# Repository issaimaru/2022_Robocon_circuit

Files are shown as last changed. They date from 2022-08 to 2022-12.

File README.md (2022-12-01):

# 2022_Robocon_circuit
**2022年ロボコンの回路**<br>
マスターブランチは保護されているので，各ブランチで必ずプルリクエストを送ってください．<br>

他にも[自作MD](https://github.com/Issaimaru/MoterDriver_v1)と[自作電源基板](https://github.com/Issaimaru/PowerSupply_v1)とか[モババ電源分岐させるやつ](https://github.com/Issaimaru/USB_JST-XH_CONVERTER)とかいろいろ使ったけど不具合多く見つかって成仏しそうになった<br>

回路図とピン配置をここに明記しておきます．<br>

- 上部機構
  - 回路図
    上部機構
    
    > **Warning**<br>
    > 回路図が一部変わっています．詳しくはIssaimaruまで...
  
  - ピン配置
  
    | ピン番号 | 機能 | 備考 |
    | :---: | :---: | :--: |
    | PB_8/D15 | I2C_SCL | MoterDriver-Controller v3との通信用(I2C)|
    | PB_9/D14 | I2C_SDA | 同様 |
    | PA_15 | UART_TX | 足回りのmbedとの通信用 |
    | PB_7 | UART_RX | 同様 |
    | PB_4/D5 | PWM1 | 上下機構のモータの制御用 |
    | PB_5/D4 | DIR1 | 同様 |
    | PB_10/D6 | PWM2 | 装填機構のモータの制御用 |
    | PB_3/D3 | DIR2 | 同様 |
    | PA_8/D7 | PWM3 | 射出機構のモータ制御用 |
    | PA_10/D2 | DIR3 | 同様 |
    | PA_1/A1 | LED1 | MDCとの通信確認用LED |
    | PA_4/A2 | LED2 | 足回りのmbedとの通信確認用LED |
    | PA_0/A0 | LED3 | 上下機構の速度確認用LED(PWMに対応) |
    | PB_0/A3 | LED4 | 上下機構の上昇確認用LED |
    | PC_1/A4 | LED5 | 上下機構の下降確認用LED |
    | PC_0/A6 | LED6 | 射出確認用LED |
    
- 足回り
  - 回路図
    足回り

    > **Warning**<br>
    > 回路図が一部変わっています．詳しくはIssaimaruまで...
    
  - ピン配置

    | ピン番号 | 機能 | 備考 |
    | :---: | :---: | :--: |
    | PB_8/D15 | I2C_SCL | MoterDriver-Controller v3との通信用(I2C)|
    | PB_9/D14 | I2C_SDA | 同様 |
    | PA_15 | TWE_TX | TWELITEとの通信用 |
    | PB_7 | TWE_RX | 同様 |
    | PA_12 | MCU_RX | 上部機構側mbedとの通信用 |
    | PA_11 | MCU_TX | 同様 |
    | PB_4/D5 | PWM1 | 三輪メカナムの正面側モータ制御用 |
    | PB_5/D4 | DIR1 | 同様 |
    | PB_10/D6 | PWM2 | 三輪メカナムの左側面側モータの制御用 |
    | PB_3/D3 | DIR2 | 同様 |
    | PA_8/D7 | PWM3 | 三輪メカナムの右側面側モータの制御用 |
    | PA_10/D2 | DIR3 | 同様 |
    | PA_0/A0 | LED1 | MDCとの通信確認用LED |
    | PA_1/A1 | LED2 | 上部機構側mbedとの通信確認用LED |
    | PA_4/A2 | LED3 | TWELITEとの通信確認用LED |
    
- 暴走対策機能付き非常停止スイッチ
  - 回路図
    暴走対策機能付き非常停止スイッチ

  - 接続方法<br>
    - INPUT1，INPUT2はPowerUnit BseriesのMILコネクタ部のうちのVCCとGNDに無理やりはんだ付けして配線を伸ばして2ピンのJST-XHで接続してください．
    - SW_INは非常停止スイッチと接続してください．
    - CTRLはPowerUnit BseriesのCTRLと接続してください．
    - SWITCHはPowerUnit BseriesのSWITCHと接続してください．
    
 - 上部機構用エンコーダー
  - 回路図
    上部機構用エンコーダー

  - ピン配置
    | ピン番号 | 機能 | 備考 |
    | :---: | :---: | :--: |
    | PB_7/D4 | I2C_SDA | メインマイコンとの通信用 |
    | PB_6/D5 | I2C_SCL | 同様 |
    | PF_0/D7 | ENC1_A | ロリコン1のA相 |
    | PF_1/D8 | ENC1_B | ロリコン1のB相 |
    | PA_8/D9 | ENC1_X | ロリコン1のX相 |
    | PA_11/D10 | ENC2_A | ロリコン2のA相 |
    | PB_5/D11 | ENC2_B | ロリコン2のB相 |
    | PB_4/D12 | ENC2_X | ロリコン2のX相 |
    | PB_1/D6 | PHOTO_OUT | フォトインタラプタの入力(HI->物体有/LOW->物体無) |
    | PA_6/A5 | RED | テープLEDの赤色点灯用ピン |
    | PA_4/A3 | GREEN | テープLEDの緑色点灯用ピン |
    | PA_3/A2 | BLUE | テープLEDの青色点灯用ピン |
    
  - 足回り用ロリコン
    - 回路図<br>
      足回り用ロリコン<br>

    - ピン配置<br>
      | ピン番号 | 機能 | 備考 |
      | :---: | :---: | :--: |
      | PB_7/D4 | I2C_SDA | メインマイコンとの通信用 |
      | PB_6/D5 | I2C_SCL | 同様 |
      | PA_12/D2 | ENC1_A | ロリコン1のA相 |
      | PB_0/D3 | ENC1_B | ロリコン1のB相 |
      | PF_0/D7 | ENC2_A | ロリコン2のA相 |
      | PB_1/D6 | ENC2_B | ロリコン2のB相 |
      | PF_1/D8 | ENC3_A | ロリコン3のA相 |
      | PA_8/D9 | ENC3_B | ロリコン3のB相 |
      | PB_5/D11 | ENC4_A | ロリコン4のA相 |
      | PA_11/D10 | ENC4_B | ロリコン4のB相 |
      
  - 国技館射出
    - 回路図<br>
      国技館射出<br>
      
    - ピン配置<br>
      | ピン番号 | 機能 | 備考 |
      | :---: | :---: | :--: |
      | PC_12 | UART1_TX | 足回りとの通信用 |
      | PD_2 | UART1_RX | 同様 |
      | 🌠PF_7 | UART2_TX | マトリクスLEDとの通信用 |
      | 🌠PF_6 | UART2_RX | 同様 |
      | 🌠PA_10 | PWM1 | モータ駆動用PWM出力ピン |
      | 🌠PB_3 | PWM2 | 同様 |
      | 🌠PB_5 | PWM3 | 同様 |
      | 🌠PB_4 | PWM4 | 同様 |
      | 🌠PA_3 | PWM5 | 同様 |
      | 🌠PA_2 | PWM6 | 同様 |
      | 🌠PC_7 | DIR1 | モータ回転方向信号出力ピン |
      | 🌠PA_9 | DIR2 | 同様 |
      | 🌠PA_8 | DIR3 | 同様 |
      | 🌠PB_10 | DIR4 | 同様 |
      | 🌠PA_7 | DIR5 | 同様 |
      | 🌠PB_6 | DIR6 | 同様 |
      | PD_5 | ENC1_B | ロリコン1のB相 |
      | PD_6 | ENC1_A | ロリコン1のA相 |
      | PD_7 | ENC2_B | ロリコン2のB相 |
      | PE_3 | ENC2_A | ロリコン2のA相 |
      | PF_1 | ENC3_B | ロリコン3のB相 |
      | PF_0 | ENC3_A | ロリコン3のA相 |
      | PD_1 | ENC4_B | ロリコン4のB相 |
      | PD_0 | ENC4_A | ロリコン4のA相 |
      | PG_0 | ENC5_B | ロリコン5のB相 |
      | PE_1 | ENC5_A | ロリコン5のA相 |
      | PG_9 | ENC6_B | ロリコン6のB相 |
      | PG_12 | ENC6_A | ロリコン6のA相 |
      | PD_14 | RED | テープLED 赤色 |
      | PD_15 | GREEN | テープLED 緑色 |
      | PE_9 | BLUE | テープLED 青色 |
      | PF_11 | LED1 | 確認用LED(任意) |
      | PE_0 | LED2 | 同様 |
      | PG_8 | LED3 | 同様 |
      | PG_5 | LED4 | 同様 |
      | PG_6 | LED5 | 同様 |

  - 国技館足回り
    - 回路図<br>
      国技館足回り<br>
      
    - ピン配置<br>
      | ピン番号 | 機能 | 備考 |
      | :---: | :---: | :--: |
      | PA_15 | UART1_TX | IM920sLとの通信用 |
      | PB_7 | UART1_RX | 同様 |
      | PA_11 | UART2_TX | 射出マイコンとの通信用 |
      | PA_12 | UART2_RX | 同様 |
      | D6/PB_10 | PWM1 | モータ駆動用PWM出力ピン |
      | D7/PA_8 | PWM2 | 同様 |
      | D8/PA_9 | PWM3 | 同様 |
      | D9/PC_7 | PWM4 | 同様 |
      | Pc_4 | DIR1 | モータ回転方向信号出力ピン |
      | PB_12 | DIR2 | 同様 |
      | PC_5 | DIR3 | 同様 |
      | PC_6 | DIR4 | 同様 |
      | PA_13 | ENC1_B | ロリコン1のB相 |
      | PA_14 | ENC1_A | ロリコン1のA相 |
      | PC_14 | ENC2_B | ロリコン2のB相 |
      | PC_15 | ENC2_A | ロリコン2のA相 |
      | PH_0 | ENC3_B | ロリコン3のB相 |
      | PH_1 | ENC3_A | ロリコン3のA相 |
      | PC_2 | ENC4_B | ロリコン4のB相 |
      | PC_3 | ENC4_A | ロリコン4のA相 |
      | A1/PA_1 | SLEEP | IM920sLのSLEEPピン |
      | A2/PA_4 | RESET | IM920sLのRESETピン |
      | A3/PB_0 | STATUS | IM920sLのSTATUSピン |
      | A4/PC_1 | XMIT | IM920sLのXMITピン |
      | A6/PC_0 | BUSY | IM920sLのBUSYピン |
      | PB_2 | LED1 | 確認用LED |
      | PB_1 | LED2 | 同様 |
      | PB_15 | LED3 | 同様 |
      | PB_14 | LED4 | 同様 |
      | PB_13 | LED5 | 同様 |
      
  - 国技館コントローラ
    - 回路図<br>
      国技館コントローラ
      
    - ピン配置<br>
      | ピン番号 | 機能 | 備考 |
      | :---: | :---: | :--: |
      | PC_10 | CK1_UP | 左十字キー↑ |
      | PC_12 | CK1_LEFT | 左十字キー← |
      | PD_2 | CK1_RIGHT | 左十字キー→ |
      | PC_11 | CK1_DOWN | 左十字キー↓ |
      | D3/PB_3 | CK2_UP | 右十字キー↑ |
      | D5/PB_4 | CK2_LEFT | 右十字キー← |
      | D4/PB_5 | CK2_RIGHT | 右十字キー→ |
      | D2/PA_10 | CK2_DOWN | 右十字キー↓ |
      | PB_14 | BL1 | 左トリガーL1 |
      | PB_13 | BL2 | 左トリガーL2 |
      | PB_1 | BR1 | 右トリガーR1 |
      | PB_15 | BR2 | 右トリガーR2 |
      | A0/PA_0 | L/R1 | 左アナログスティックx軸 |
      | A1/PA_1 | U/D1 | 左アナログスティックy軸 |
      | A2/PA_4 | L/R2 | 右アナログスティックx軸 |
      | A3/PB_0 | U/D2 | 右アナログスティックy軸 |
      | PA_13 | EME_SW | 非常停止スイッチ入力(HIGH:開 LOW:閉) |
      | PA_15 | TX | IM920sL通信用 |
      | PB_7 | RX | 同様 |
      | PH_1 | XMIT | IM920sLのドキュメント参照 |
      | PC_2 | SLEEP | 同様 |
      | PC_3 | STATUS | 同様 |
      | A6/PC_0 | BUSY | 同様 |
      | A4/PC_1 | RESET | 同様 |
      | D14/PB_9 | LED1 | 確認用LED |
      | D15/PB_8 | LED2 | 同様 |
      | PC_9 | LED3 | 同様 | 
      | PC_8 | LED4 | 同様 |
      | PC_6 | LED5 | 同様 |

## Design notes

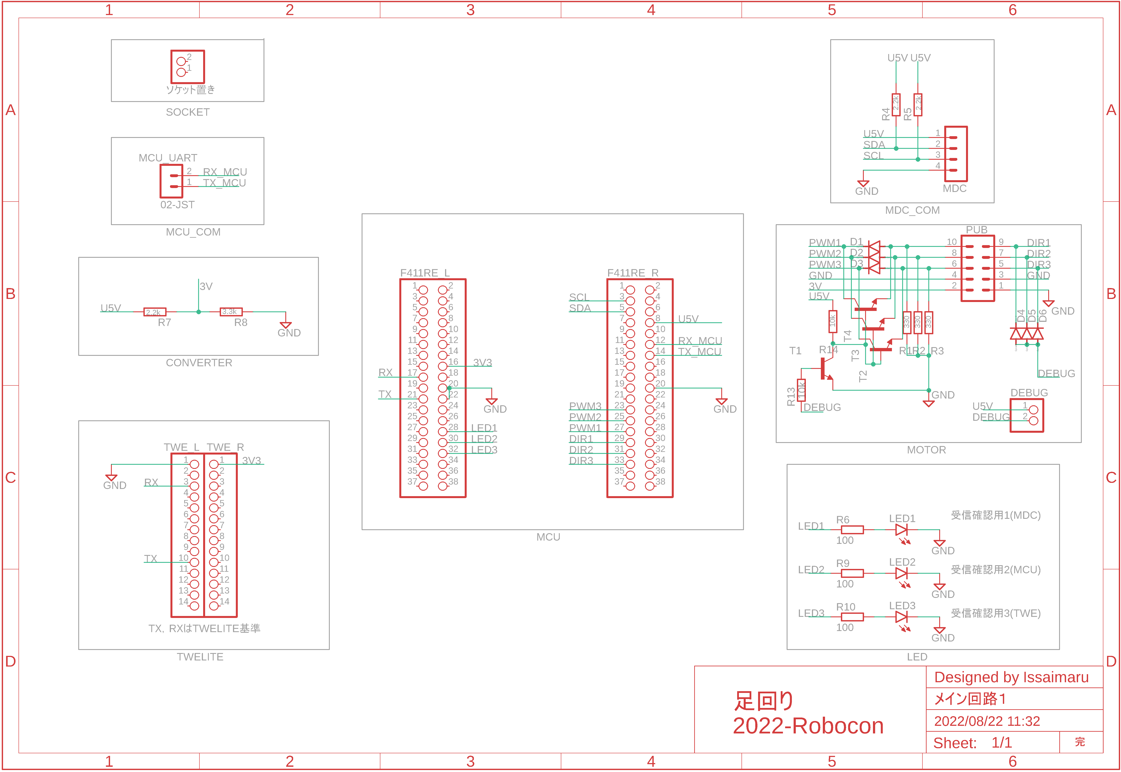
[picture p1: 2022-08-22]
Image/足回り.png

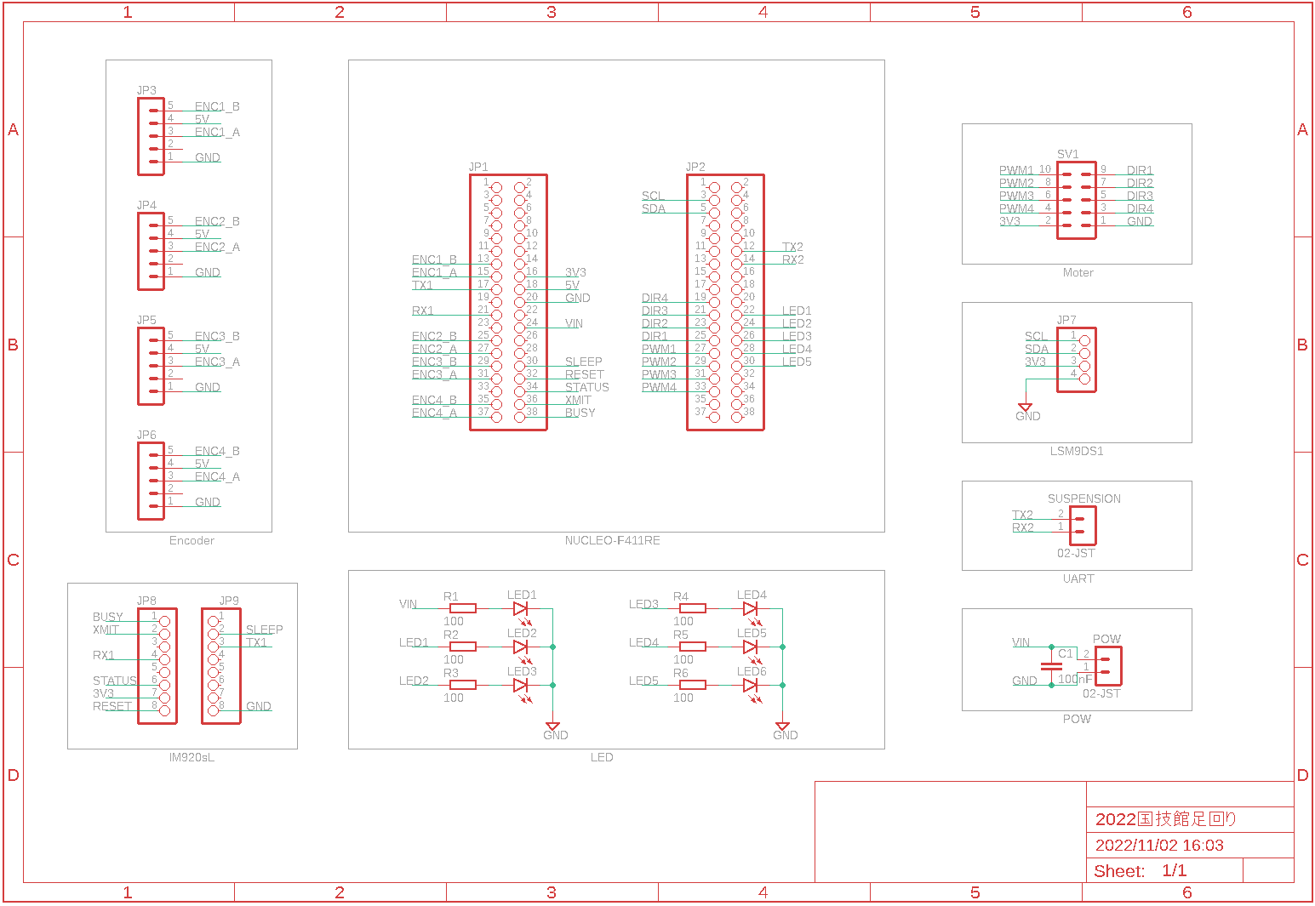
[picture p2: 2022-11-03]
Image/国技館足回り.png

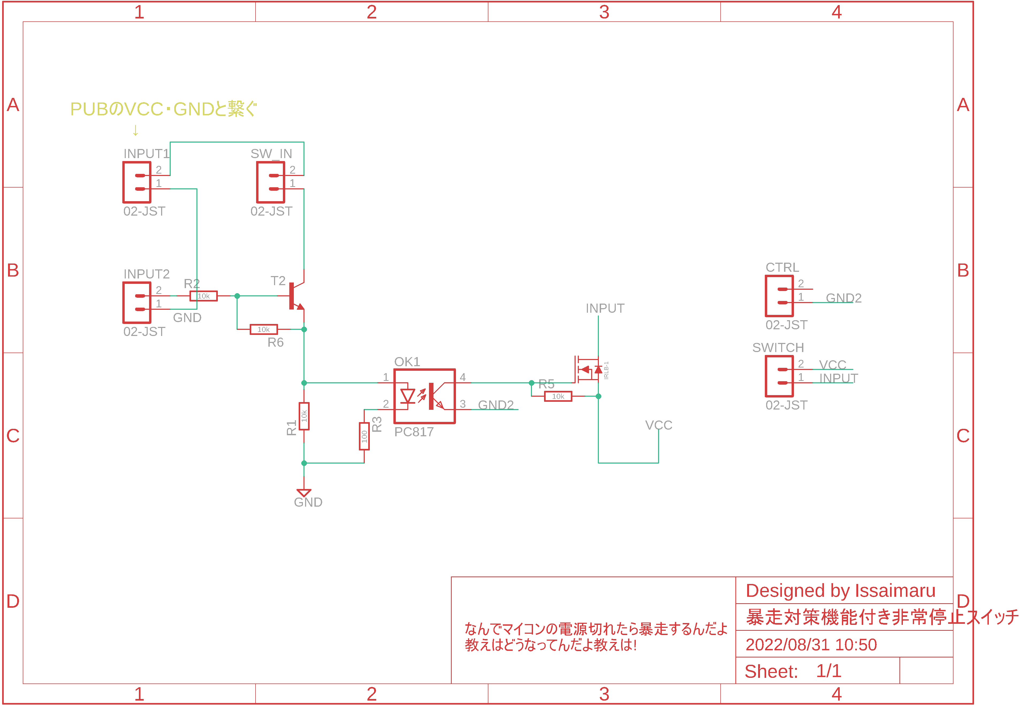
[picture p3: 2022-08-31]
Image/暴走対策機能付き非常停止スイッチ.png

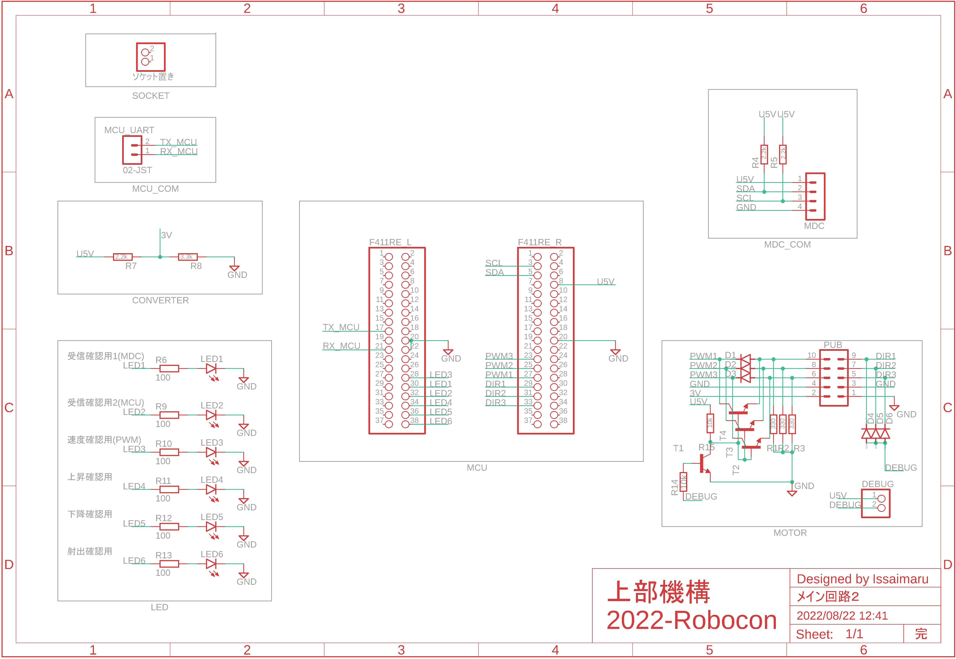
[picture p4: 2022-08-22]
Image/上部機構.png

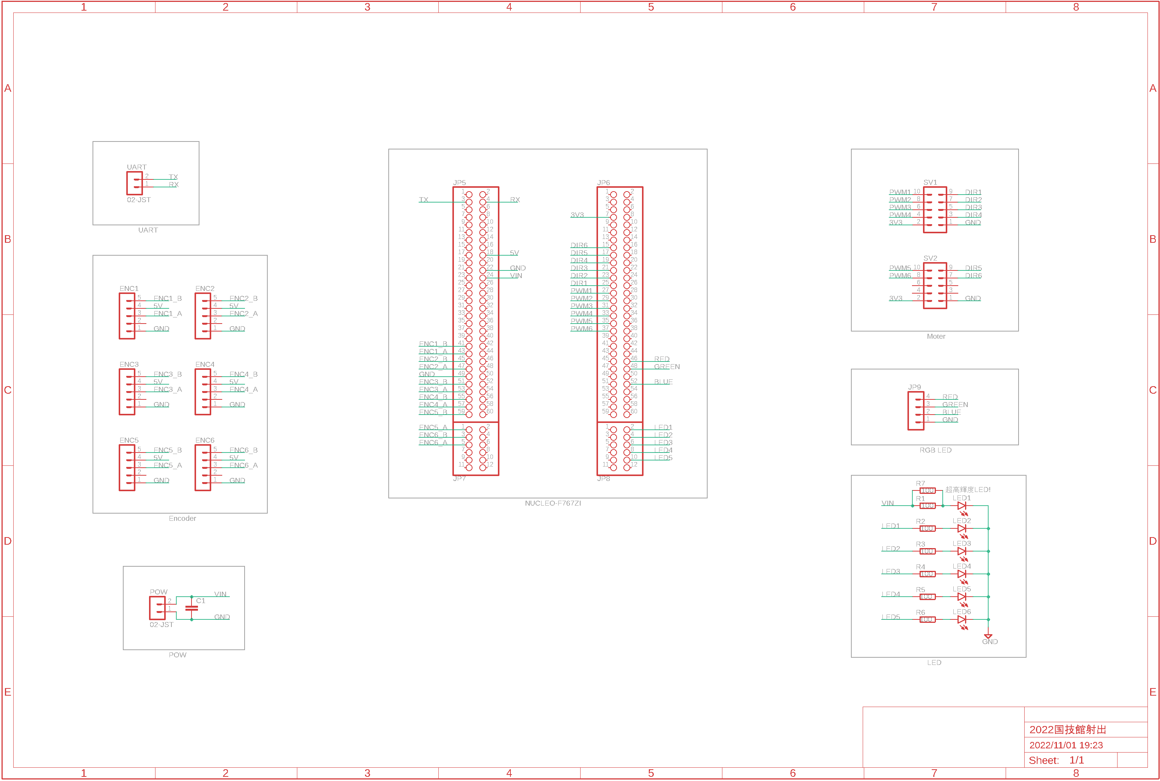
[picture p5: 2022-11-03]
Image/国技館射出.png

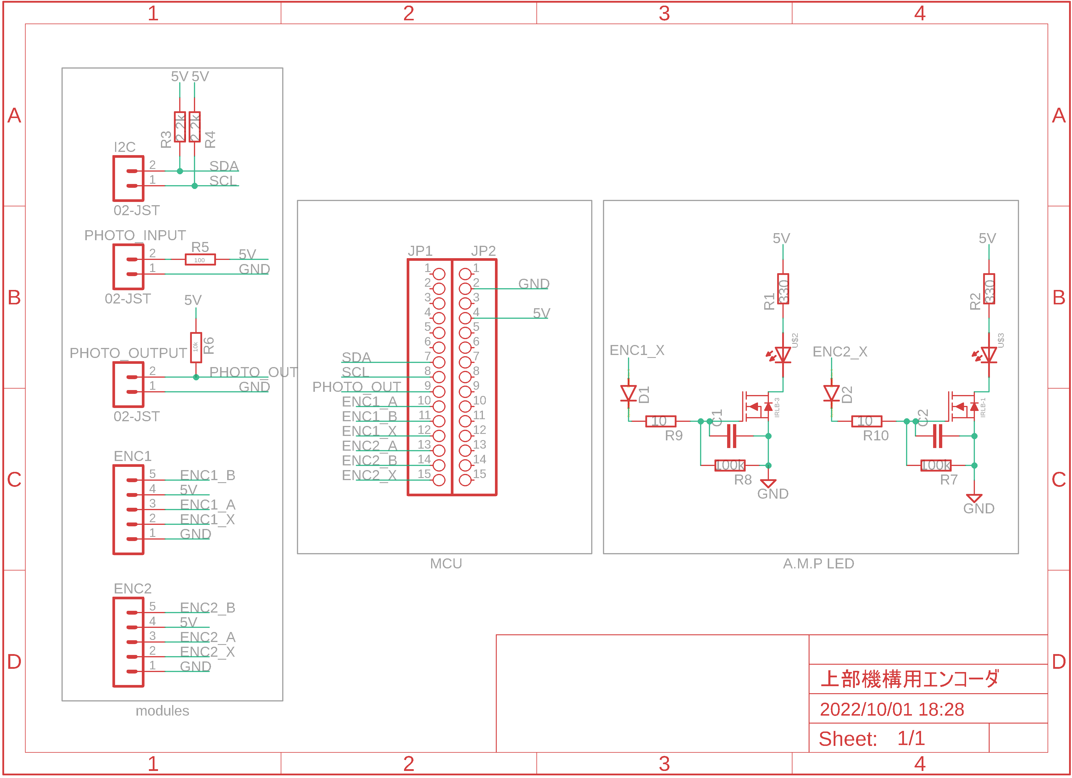
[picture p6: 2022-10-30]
src/上部機構用エンコーダー.png

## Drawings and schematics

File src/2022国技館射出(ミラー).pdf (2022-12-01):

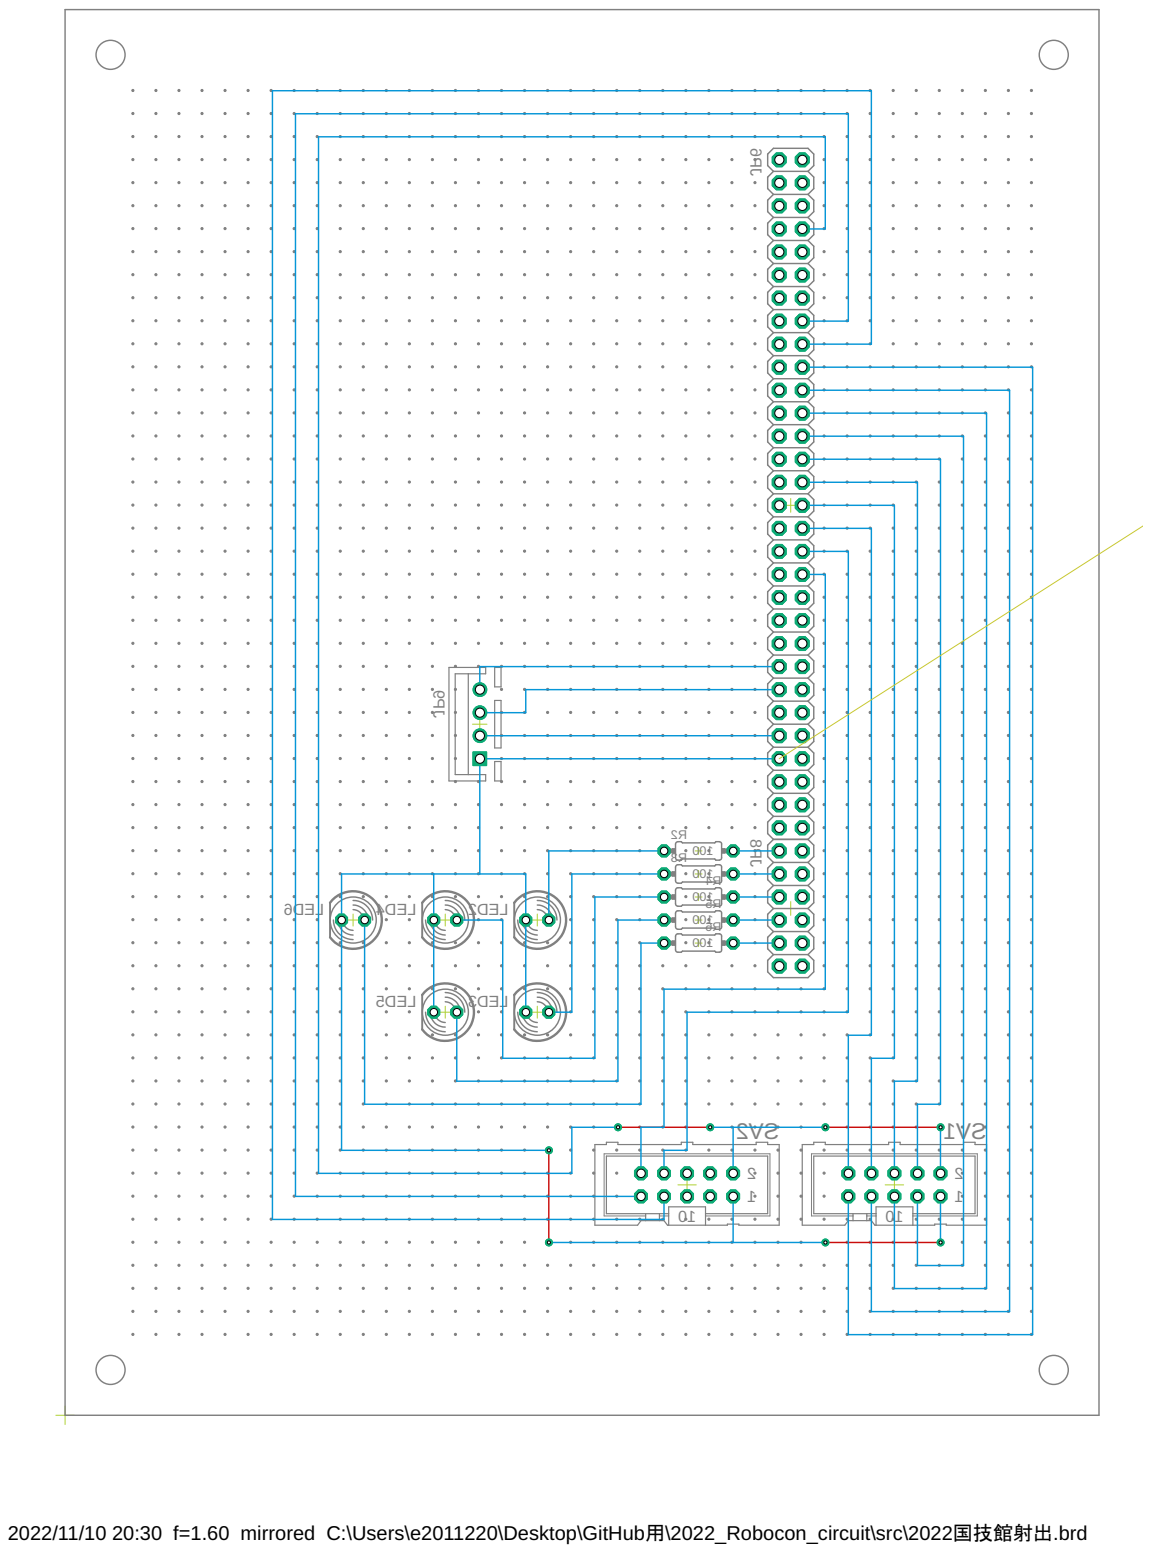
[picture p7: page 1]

2022/11/10 20:30 f=1.60 mirrored C:\Users\e2011220\Desktop\GitHub用\2022_Robocon_circuit\src\2022国技館射出.brd

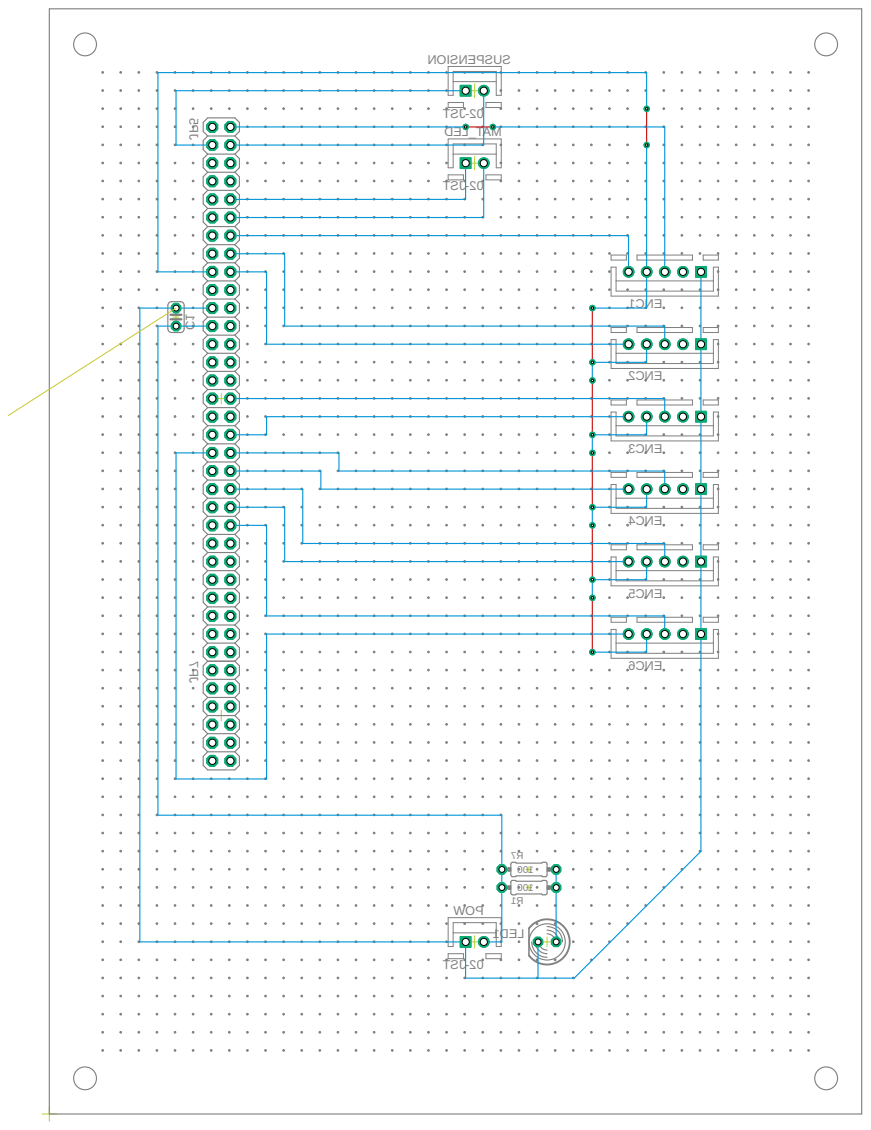
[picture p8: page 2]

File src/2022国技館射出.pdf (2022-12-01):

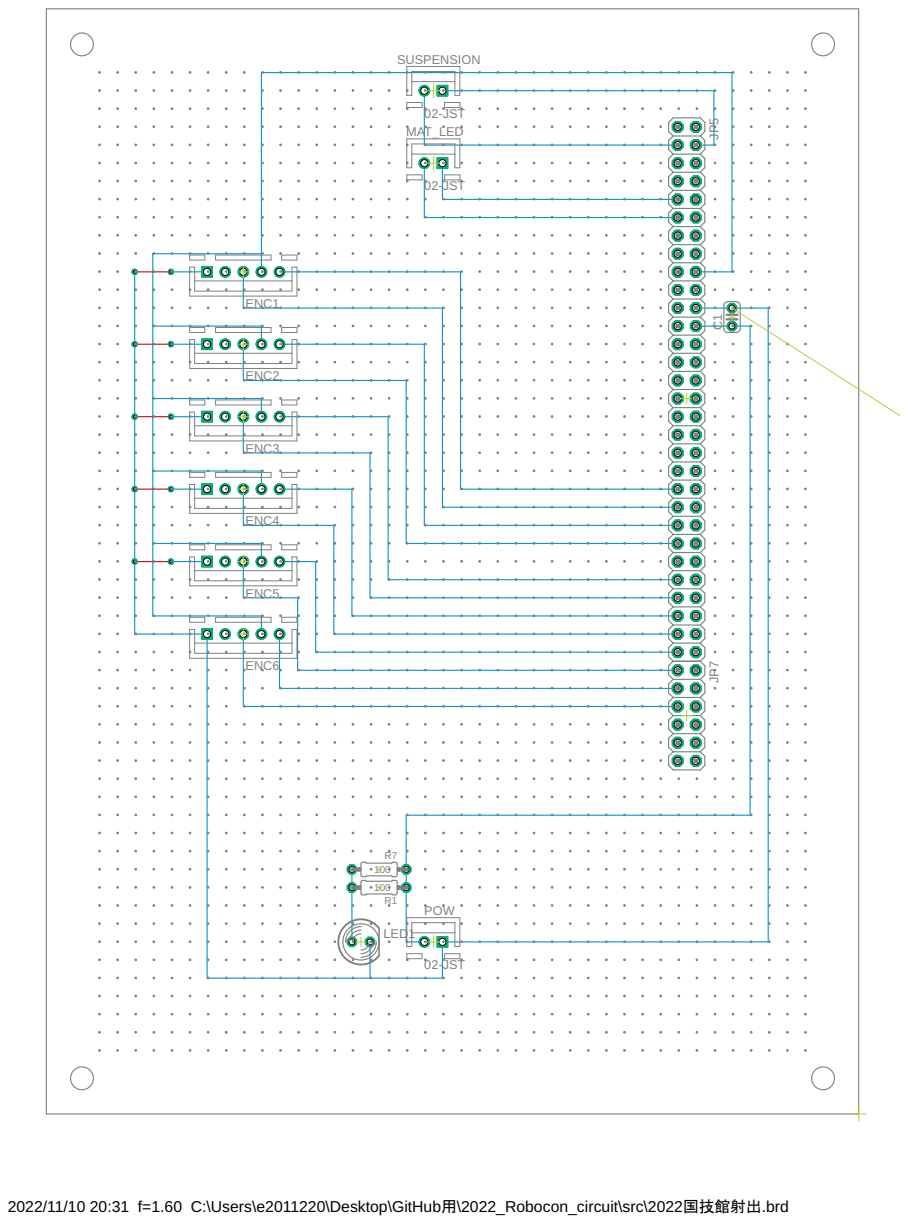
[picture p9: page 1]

2022/11/10 20:31 f=1.60 C:\Users\e2011220\Desktop\GitHub用\2022_Robocon_circuit\src\2022国技館射出.brd

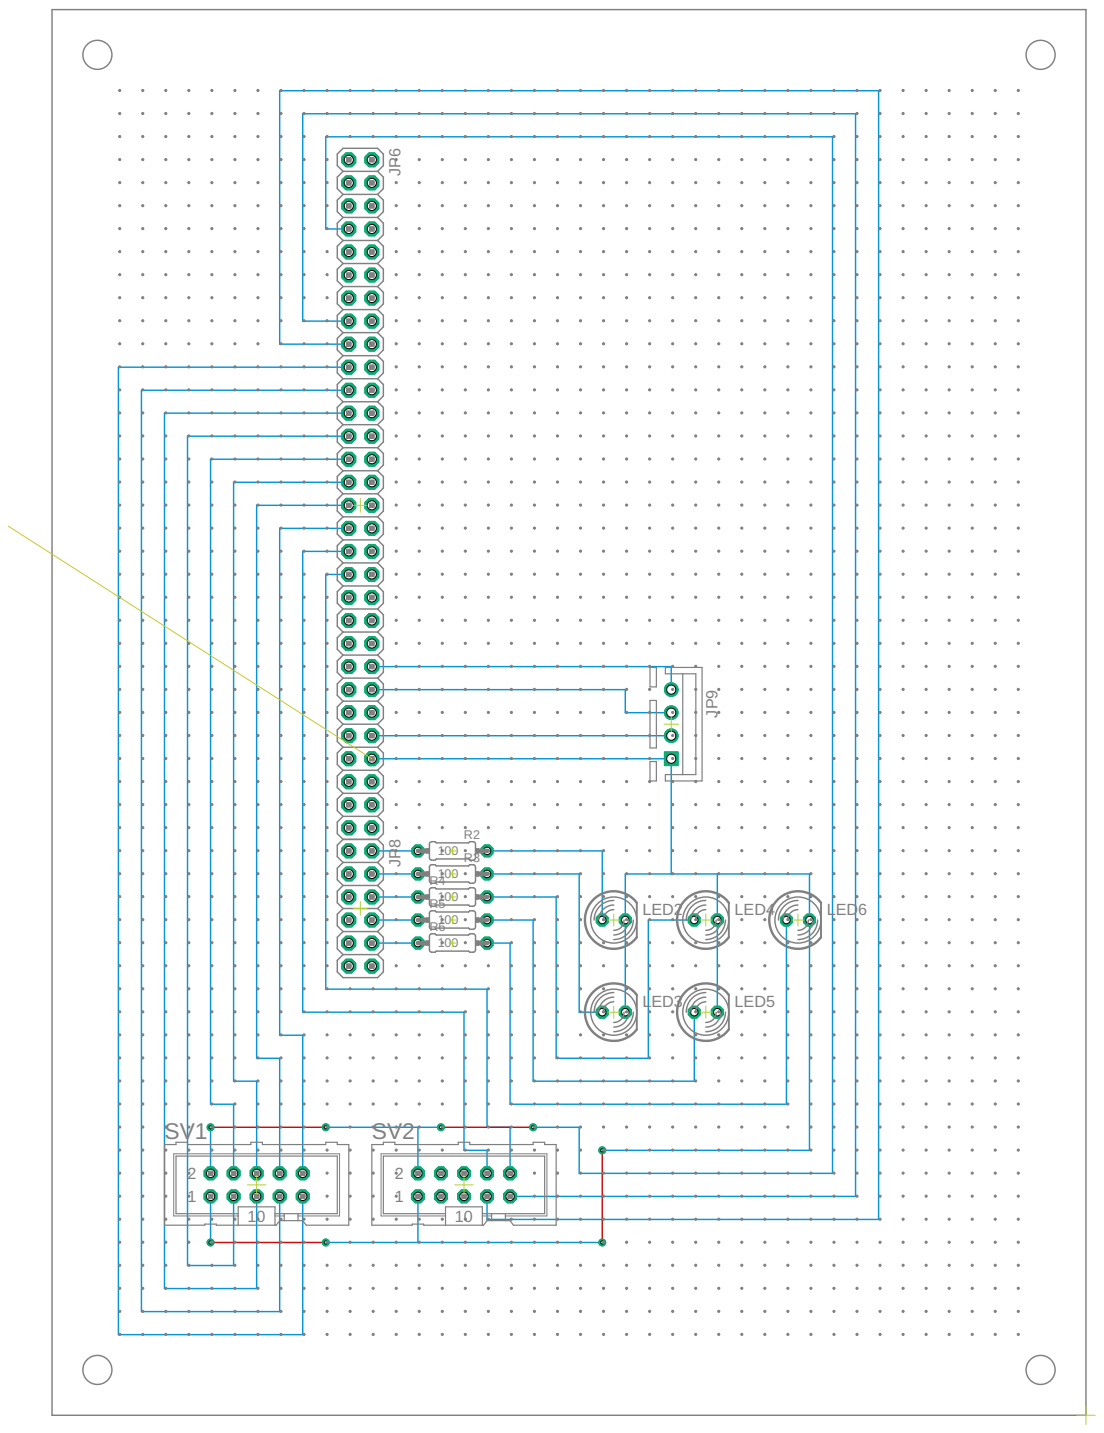
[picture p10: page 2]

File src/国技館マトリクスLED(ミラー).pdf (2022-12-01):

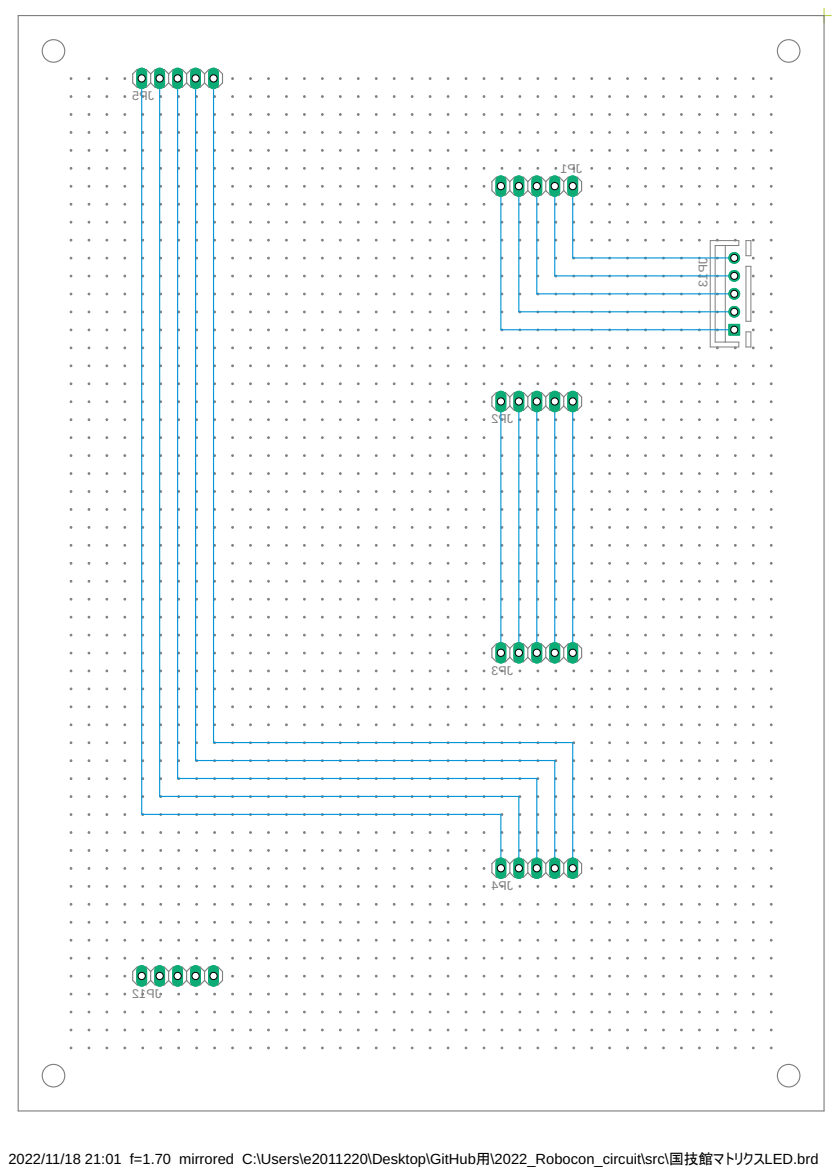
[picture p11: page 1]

2022/11/18 21:01 f=1.70 mirrored C:\Users\e2011220\Desktop\GitHub用\2022_Robocon_circuit\src\国技館マトリクスLED.brd

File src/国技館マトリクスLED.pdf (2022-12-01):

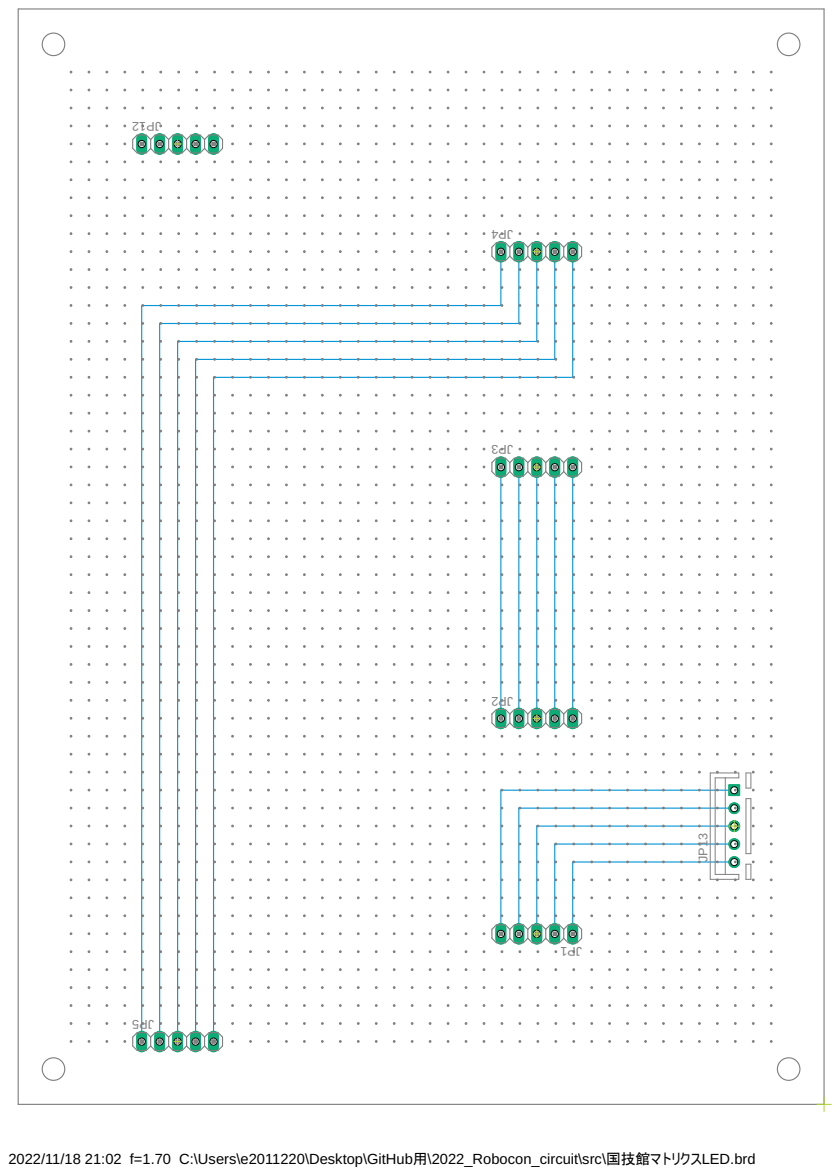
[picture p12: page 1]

2022/11/18 21:02 f=1.70 C:\Users\e2011220\Desktop\GitHub用\2022_Robocon_circuit\src\国技館マトリクスLED.brd

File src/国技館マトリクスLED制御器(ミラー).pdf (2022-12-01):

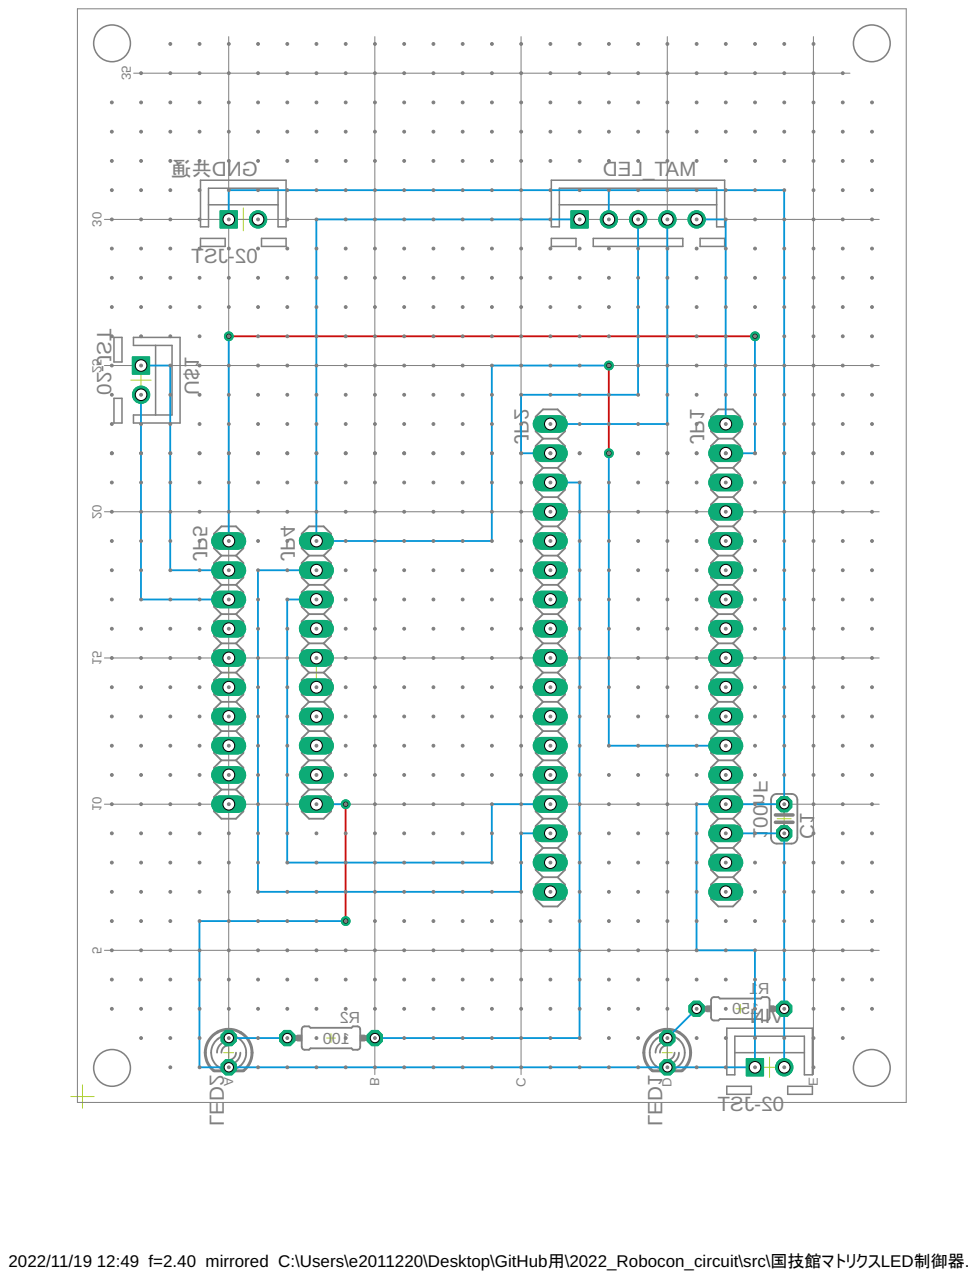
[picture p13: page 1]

2022/11/19 12:49 f=2.40 mirrored C:\Users\e2011220\Desktop\GitHub用\2022_Robocon_circuit\src\国技館マトリクスLED制御器.brd

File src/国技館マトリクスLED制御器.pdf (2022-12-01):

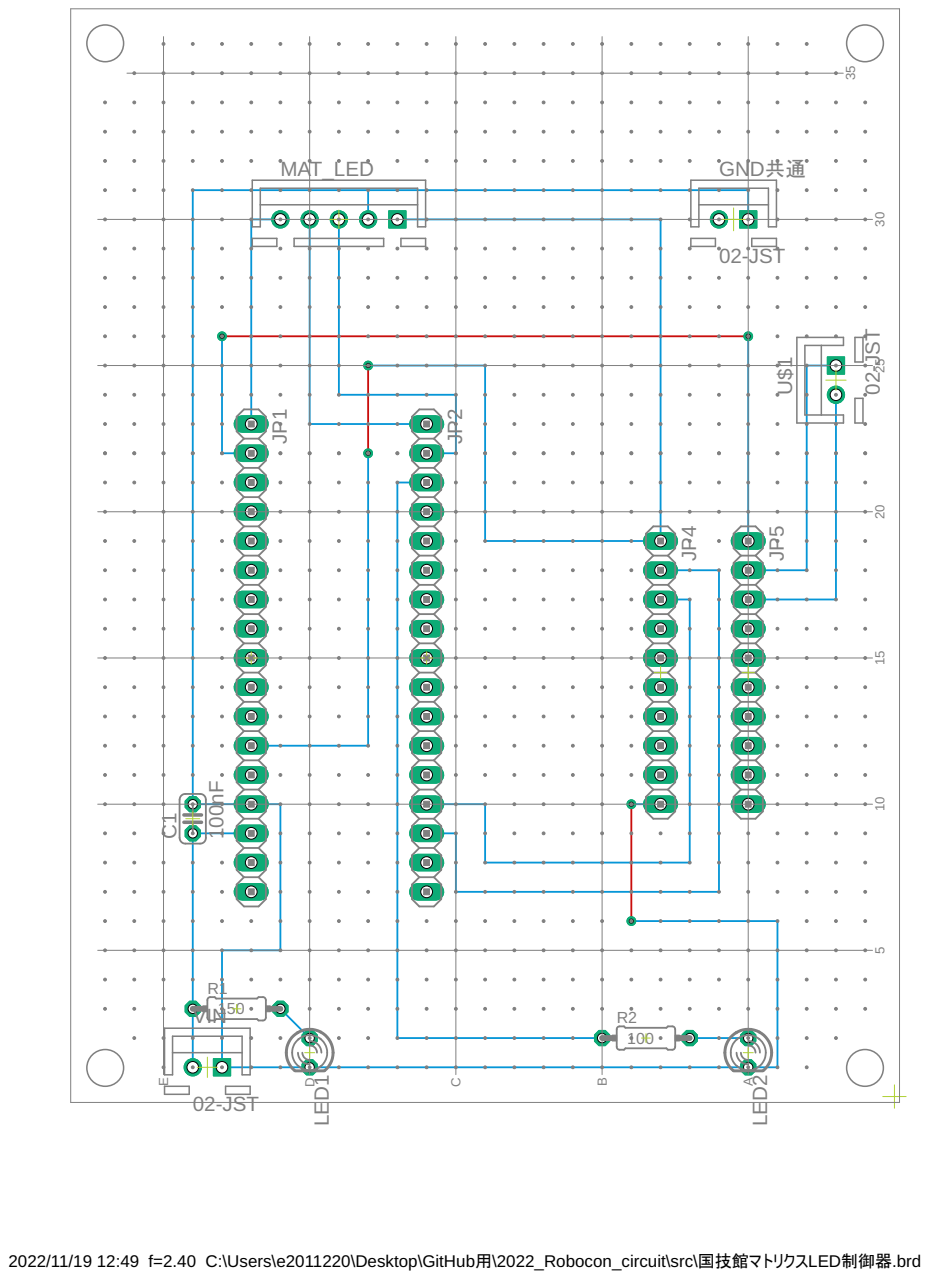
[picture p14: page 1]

2022/11/19 12:49 f=2.40 C:\Users\e2011220\Desktop\GitHub用\2022_Robocon_circuit\src\国技館マトリクスLED制御器.brd

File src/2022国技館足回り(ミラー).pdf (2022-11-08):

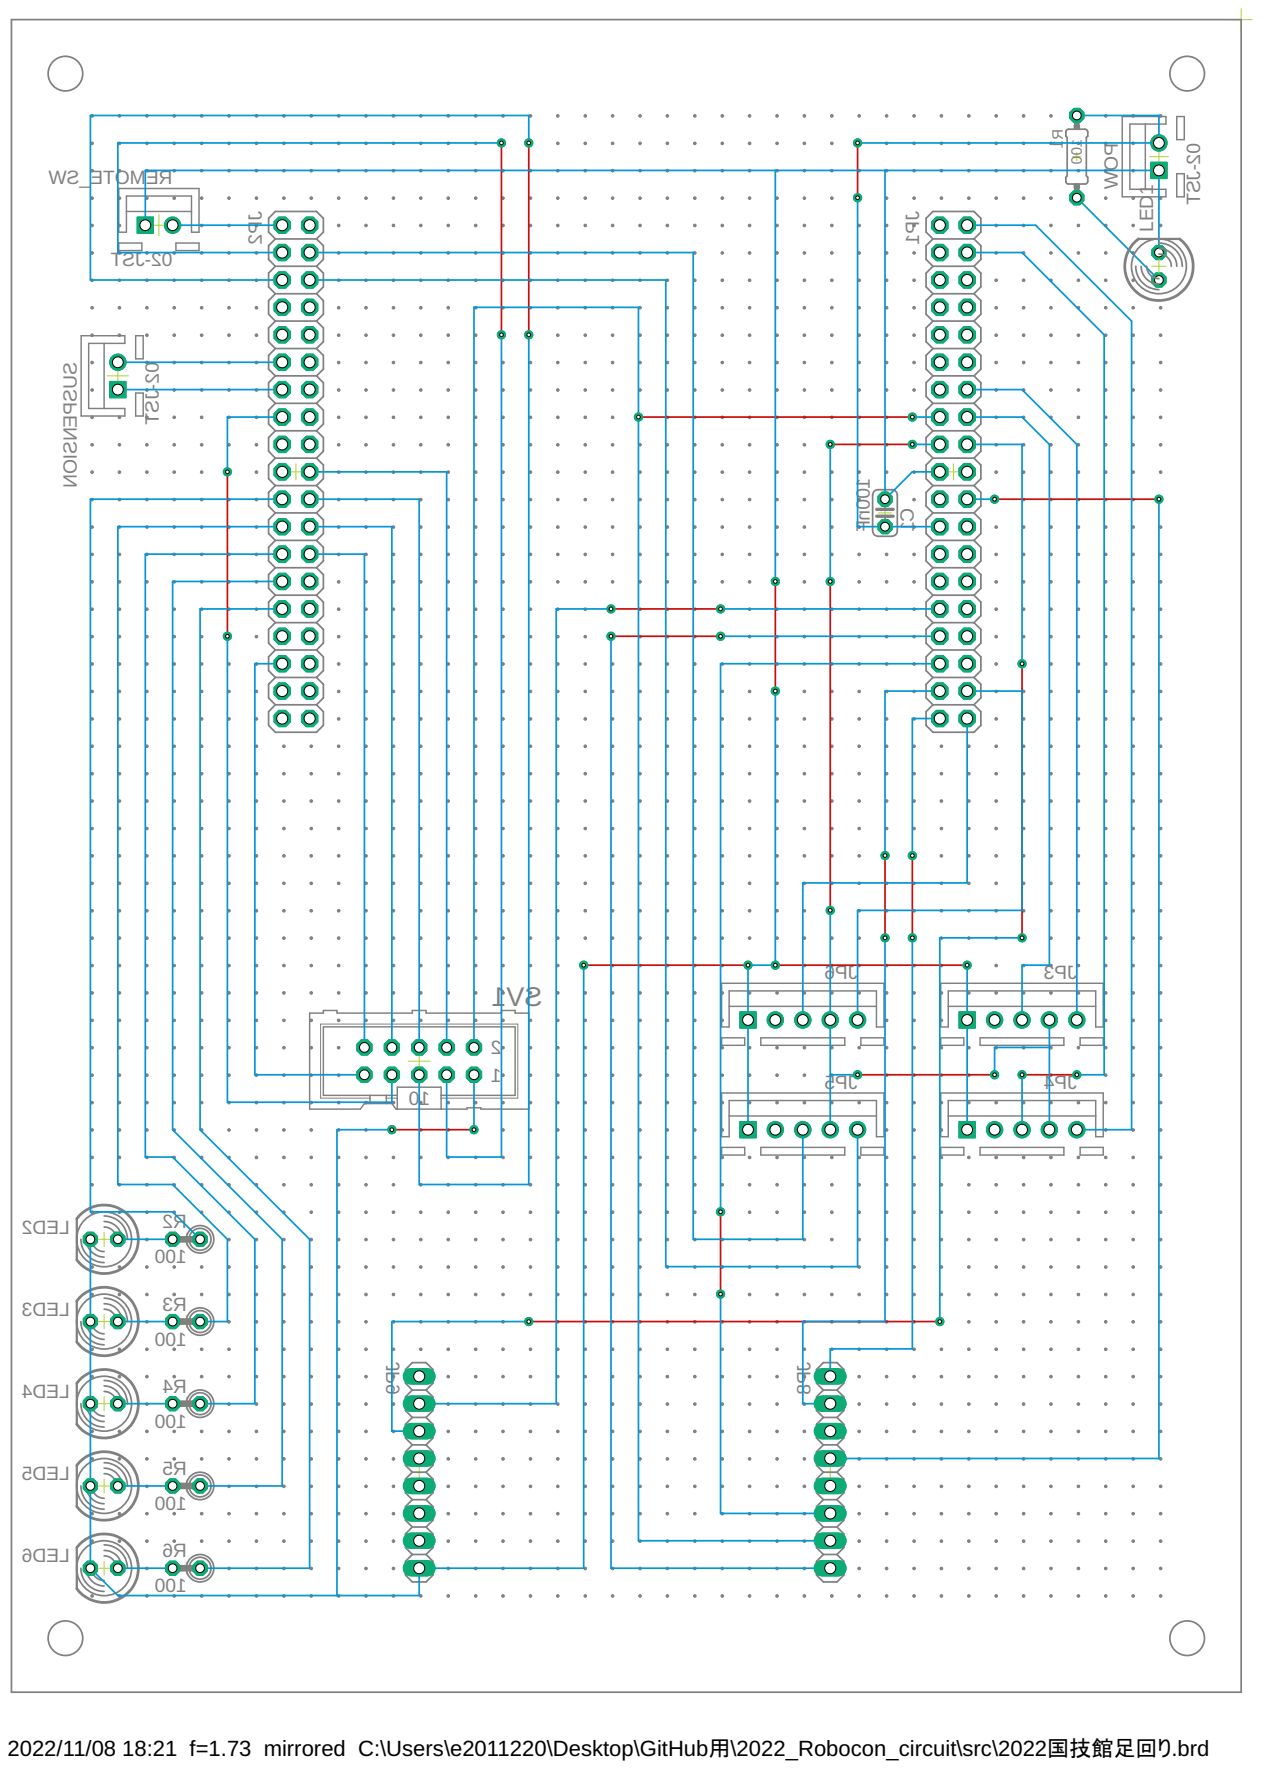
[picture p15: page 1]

2022/11/08 18:21 f=1.73 mirrored C:\Users\e2011220\Desktop\GitHub用\2022_Robocon_circuit\src\2022国技館足回り.brd

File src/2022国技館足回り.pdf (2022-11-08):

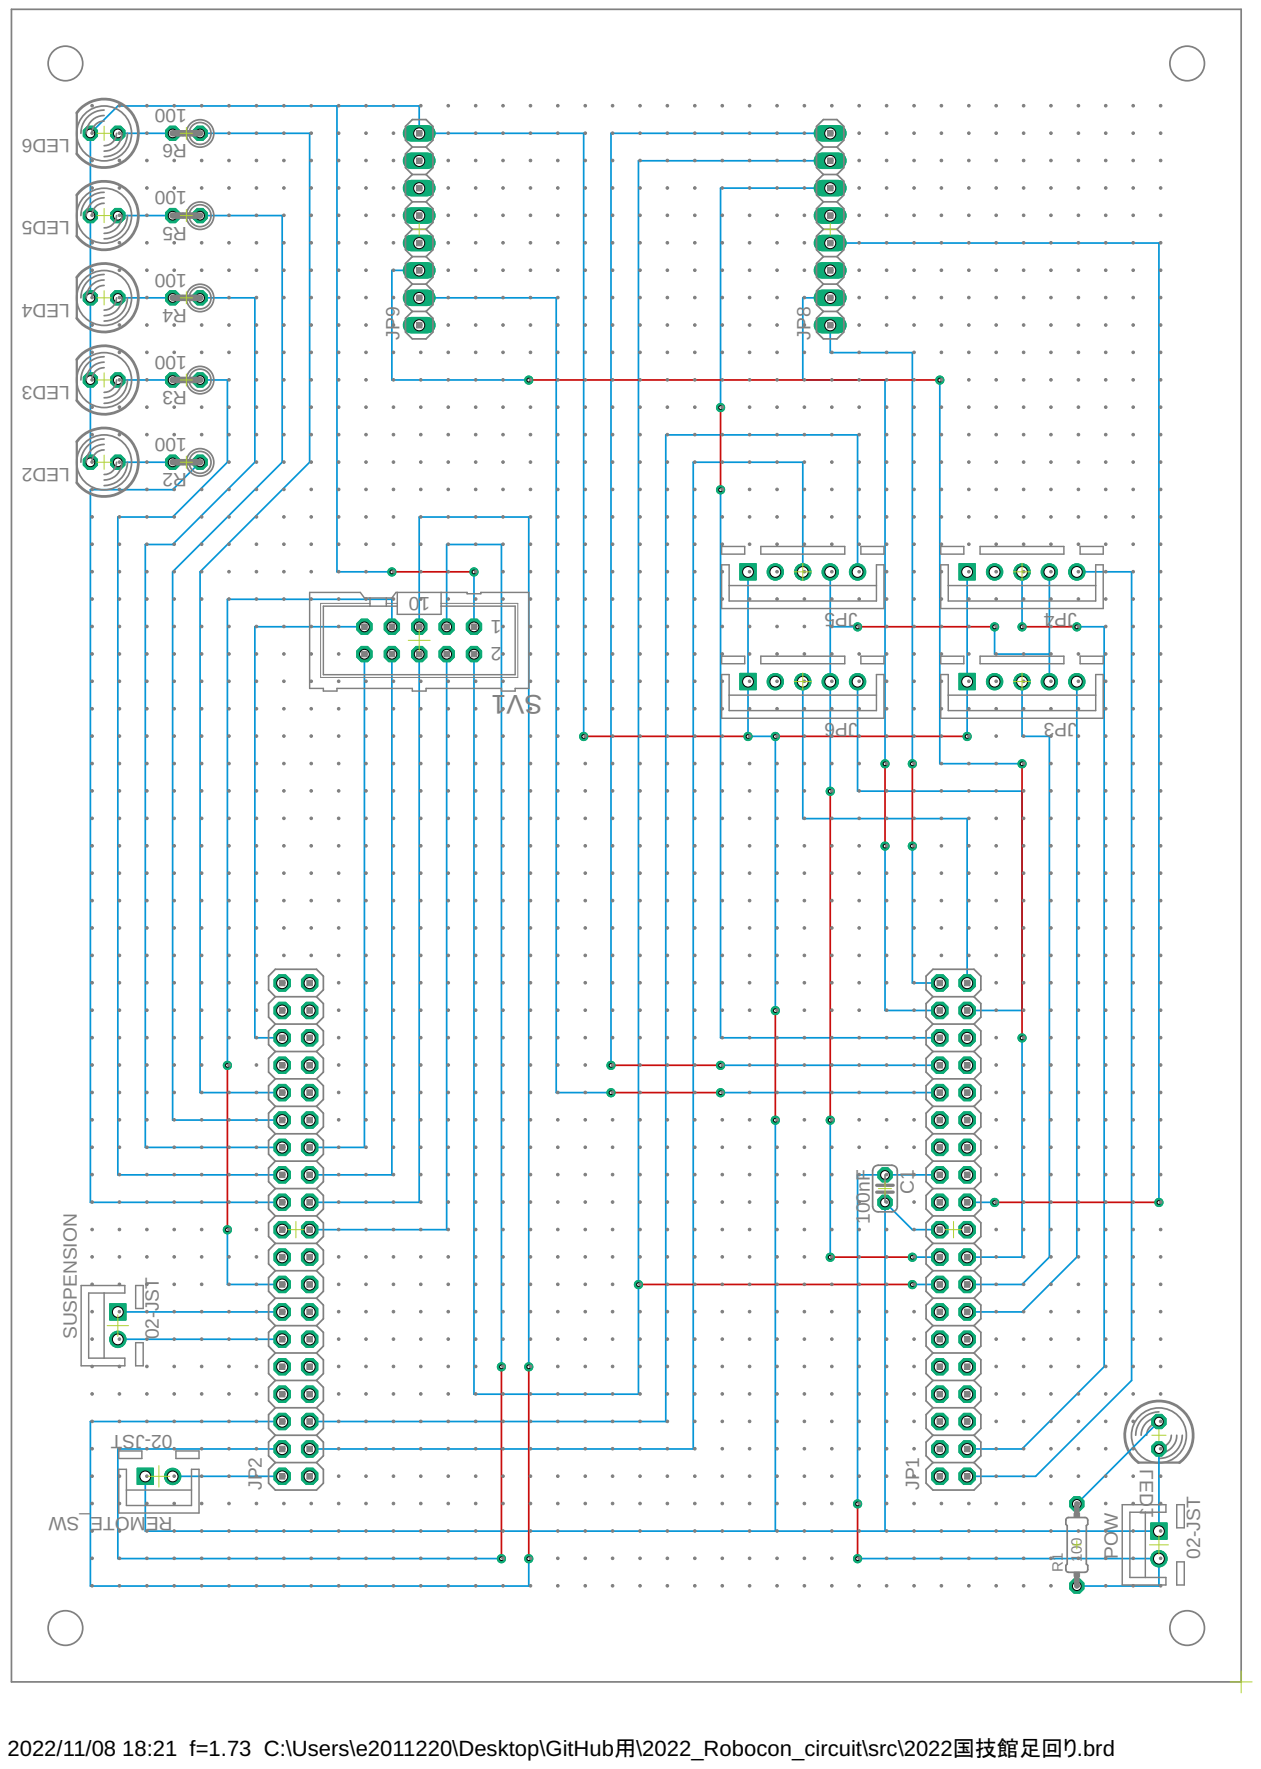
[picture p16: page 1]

2022/11/08 18:21 f=1.73 C:\Users\e2011220\Desktop\GitHub用\2022_Robocon_circuit\src\2022国技館足回り.brd

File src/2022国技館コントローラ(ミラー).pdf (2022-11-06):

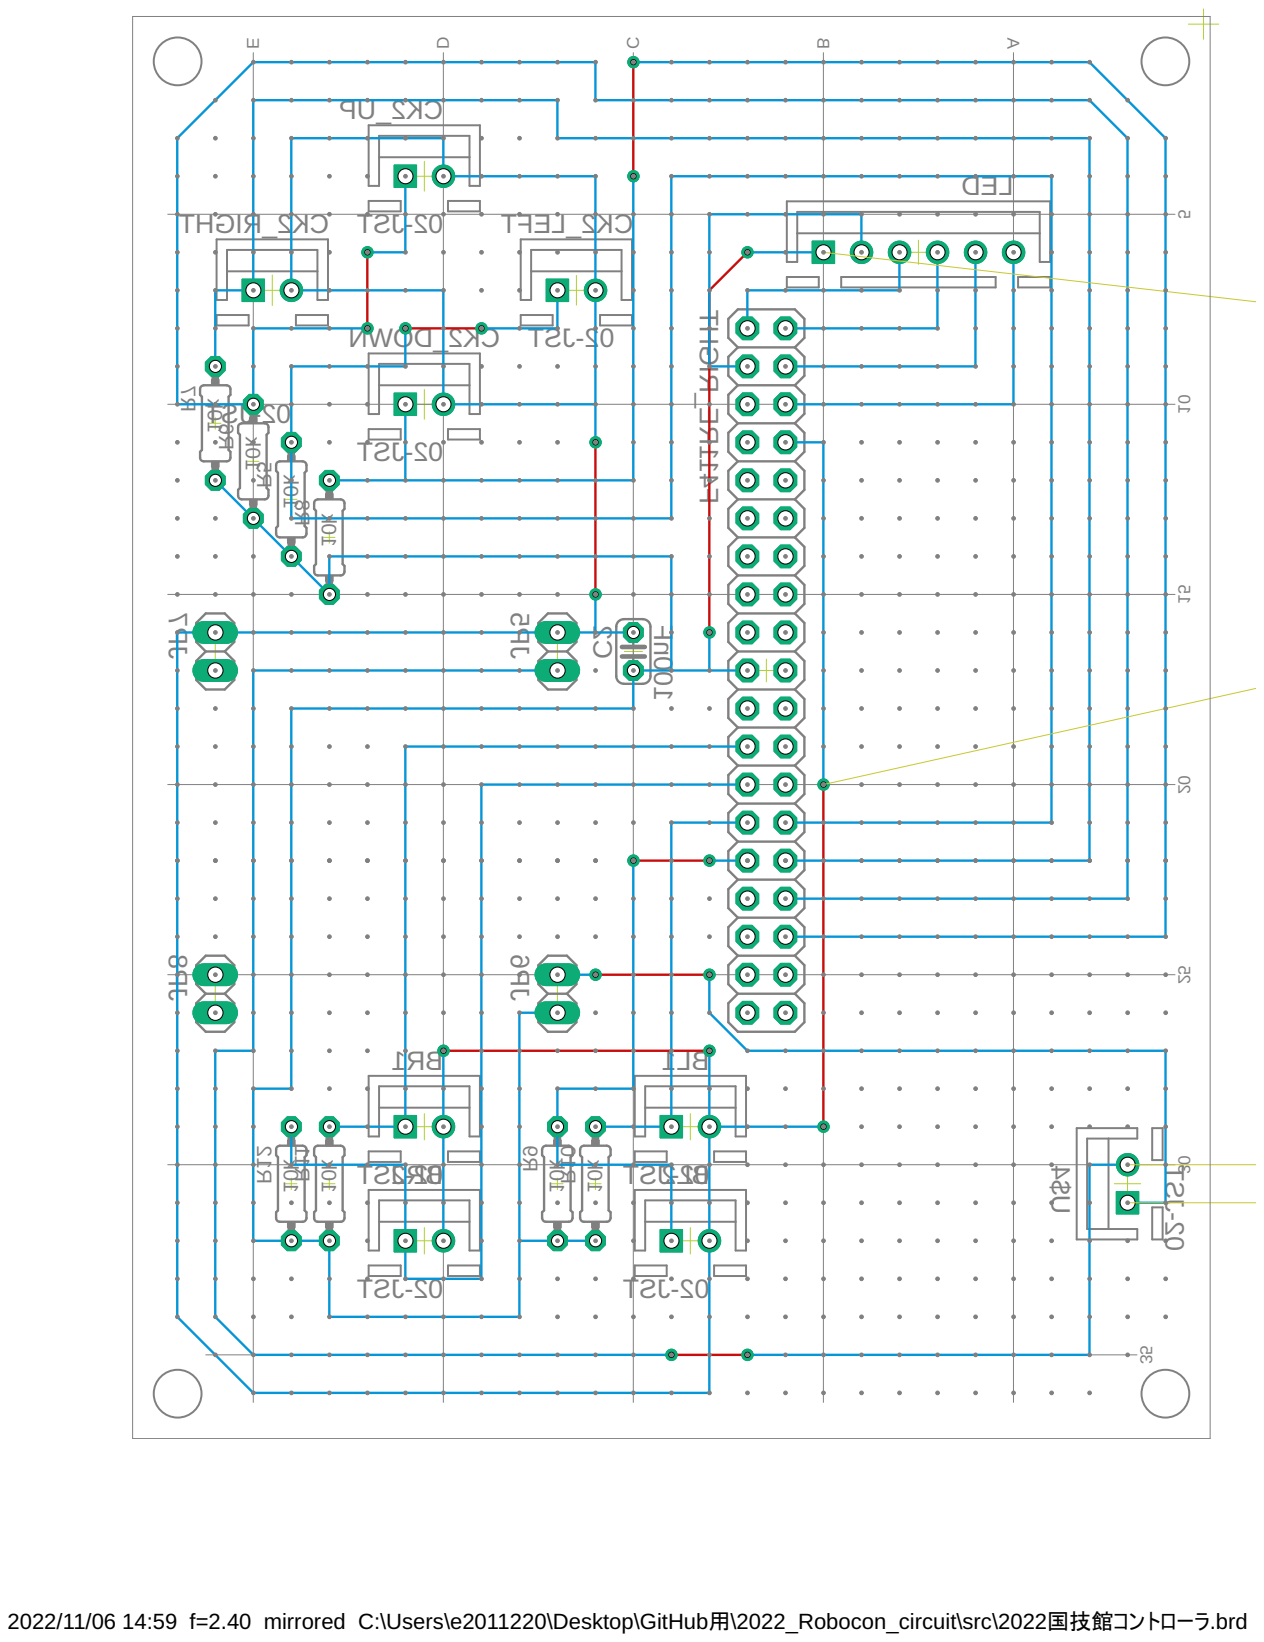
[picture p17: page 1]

2022/11/06 14:59 f=2.40 mirrored C:\Users\e2011220\Desktop\GitHub用\2022_Robocon_circuit\src\2022国技館コントローラ.brd

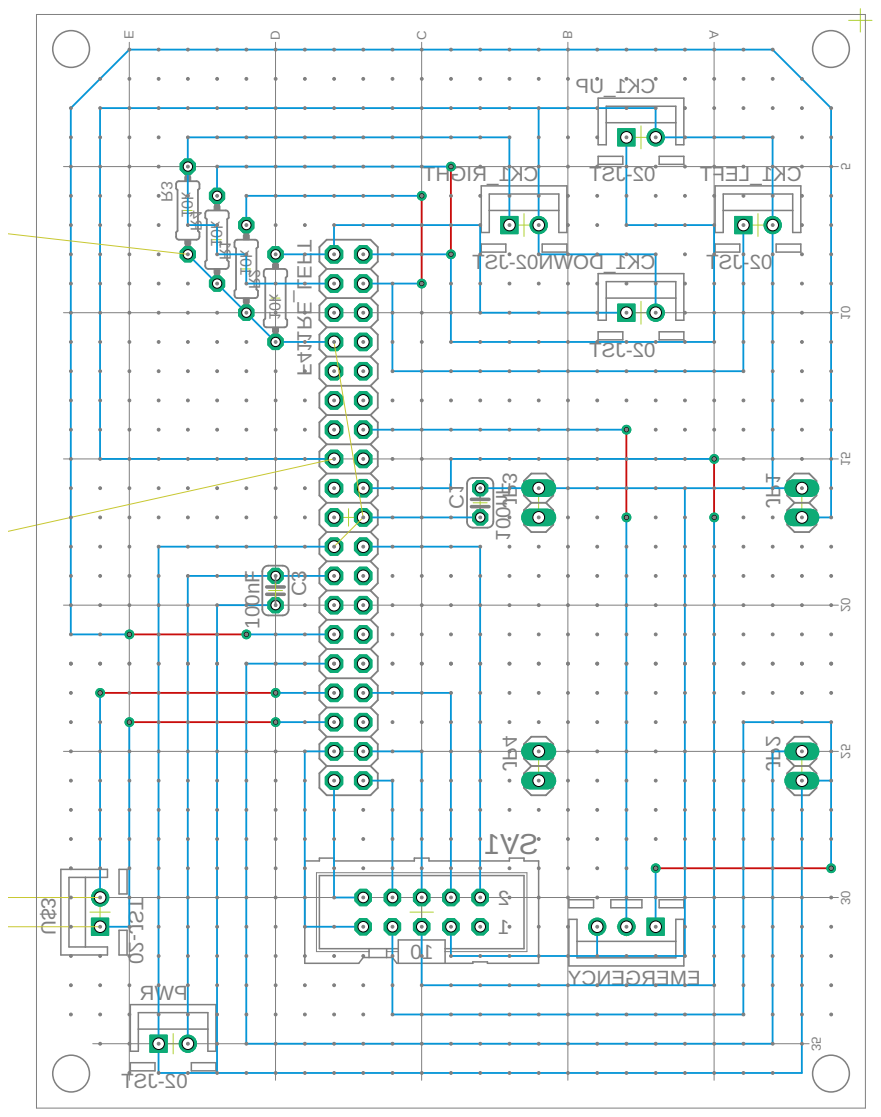
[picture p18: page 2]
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

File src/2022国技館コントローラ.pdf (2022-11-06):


2022/11/06 14:59 f=2.40 C:\Users\e2011220\Desktop\GitHub用\2022_Robocon_circuit\src\2022国技館コントローラ.brd


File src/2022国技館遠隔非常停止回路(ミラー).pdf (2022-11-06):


2022/11/06 11:47 f=2.40 mirrored C:\Users\e2011220\Desktop\GitHub用\2022_Robocon_circuit\src\2022国技館遠隔非常停止回路.brd

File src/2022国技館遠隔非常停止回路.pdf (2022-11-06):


2022/11/06 11:47 f=2.40 C:\Users\e2011220\Desktop\GitHub用\2022_Robocon_circuit\src\2022国技館遠隔非常停止回路.brd

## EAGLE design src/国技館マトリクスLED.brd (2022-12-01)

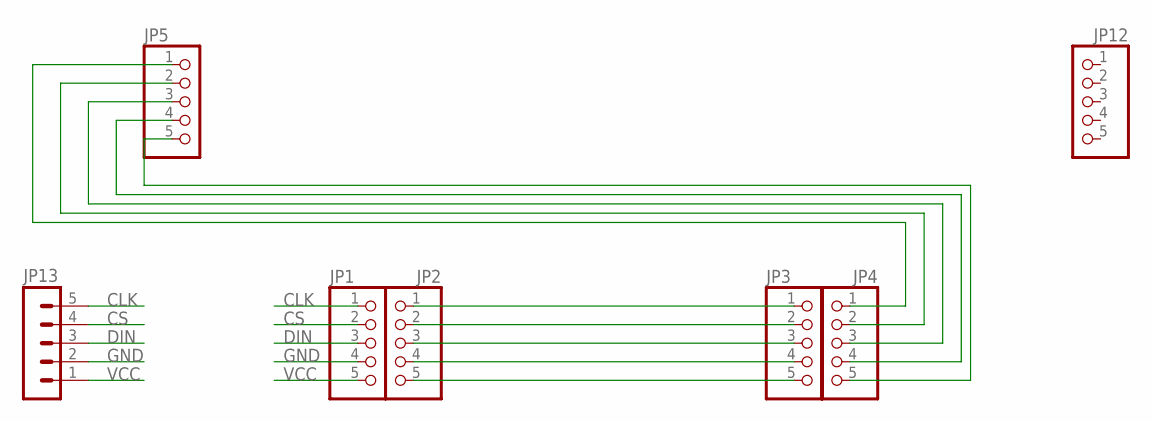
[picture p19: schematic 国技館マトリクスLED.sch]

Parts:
JP1, JP2, JP3, JP4, JP5, JP12: PINHD-1X5; 1X05
JP13: 05-JST; B5B-XH

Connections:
CLK: JP1.1, JP13.5
CS: JP1.2, JP13.4
DIN: JP1.3, JP13.3
GND: JP1.4, JP13.2
unnamed: JP2.1, JP3.1
unnamed: JP2.2, JP3.2
unnamed: JP2.3, JP3.3
unnamed: JP2.4, JP3.4
unnamed: JP2.5, JP3.5
unnamed: JP4.1, JP5.1
unnamed: JP4.2, JP5.2
unnamed: JP4.3, JP5.3
unnamed: JP4.4, JP5.4
unnamed: JP4.5, JP5.5
VCC: JP1.5, JP13.1

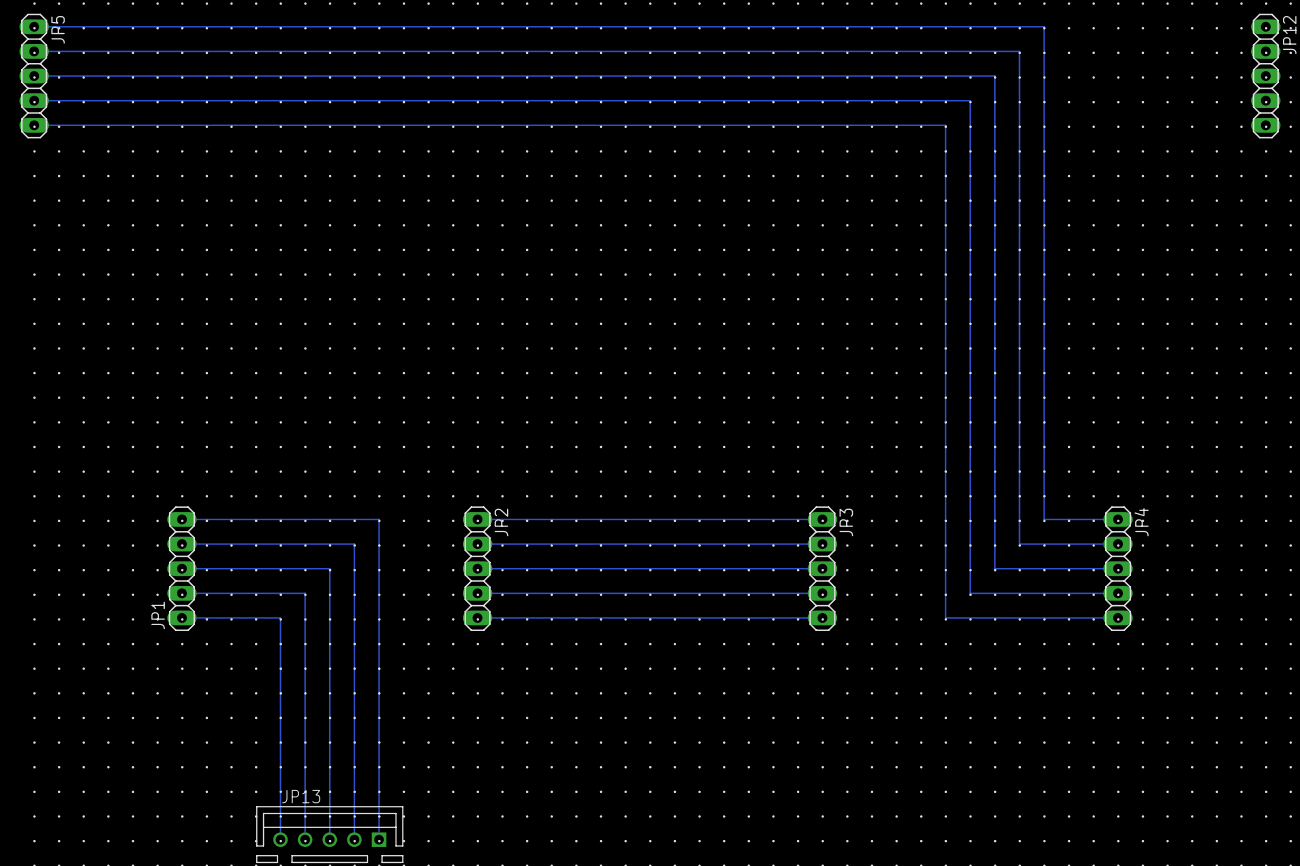
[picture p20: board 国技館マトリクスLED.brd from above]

Board: 2 copper layers, 8 parts (0 on the bottom side), 15 nets.

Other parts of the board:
U$1: TYPE.A

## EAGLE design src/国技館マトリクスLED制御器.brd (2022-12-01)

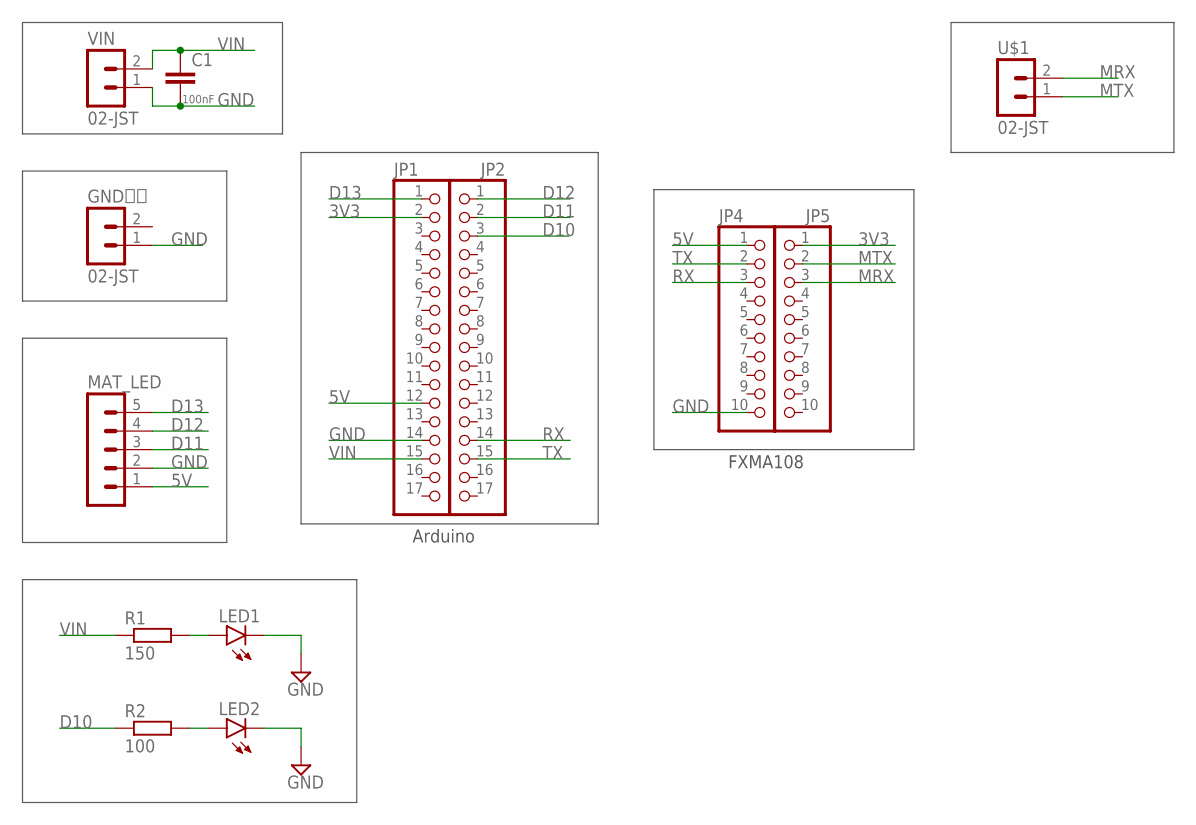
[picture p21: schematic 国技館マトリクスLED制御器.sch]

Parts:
C1: 100nF; C025-024X044
GND共通: 02-JST; B2B-XH
JP1, JP2: PINHD-1X17; 1X17
JP4, JP5: PINHD-1X10; 1X10
LED1, LED2: LED3MM
MAT_LED: 05-JST; B5B-XH
R1: 150; 0204/7
R2: 100; 0204/7
U$1: 02-JST; B2B-XH
VIN: 02-JST; B2B-XH

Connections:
3V3: JP1.2, JP5.1
5V: JP1.12, JP4.1, MAT_LED.1
D10: JP2.3, R2.1
D11: JP2.2, MAT_LED.3
D12: JP2.1, MAT_LED.4
D13: JP1.1, MAT_LED.5
GND: C1.2, GND共通.1, JP1.14, JP4.10, LED1.K (C), LED2.K (C), MAT_LED.2, VIN.1
MRX: JP5.3, U$1.2
MTX: JP5.2, U$1.1
unnamed: LED1.A, R1.2
unnamed: LED2.A, R2.2
RX: JP2.14, JP4.3
TX: JP2.15, JP4.2
VIN: C1.1, JP1.15, R1.1, VIN.2

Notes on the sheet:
FXMA108
Arduino

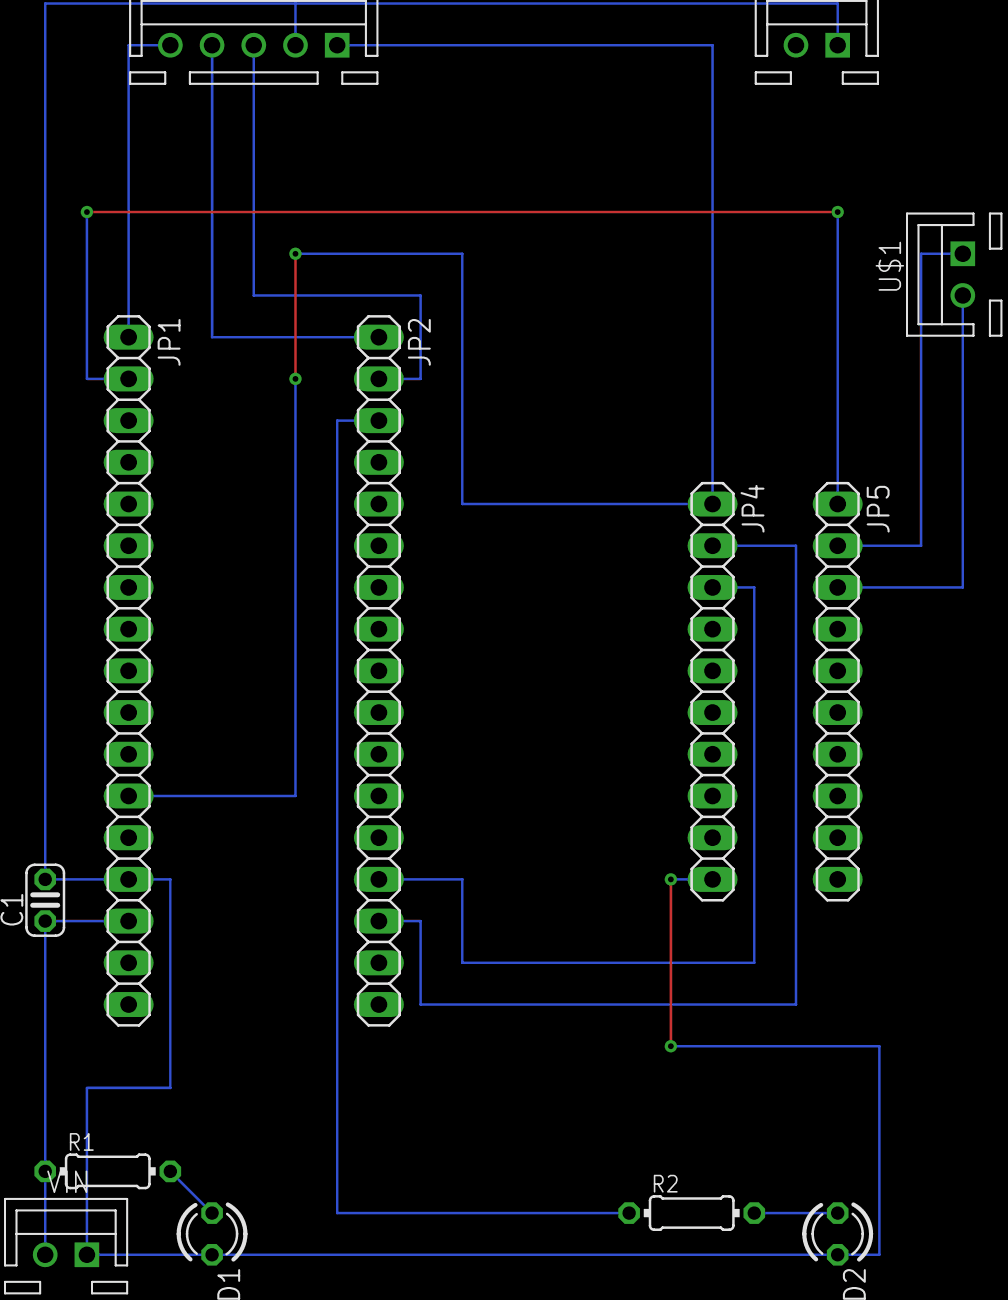
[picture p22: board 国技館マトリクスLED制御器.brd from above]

Board: 2 copper layers, 14 parts (0 on the bottom side), 14 nets.

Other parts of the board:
U$2: TYPE.B

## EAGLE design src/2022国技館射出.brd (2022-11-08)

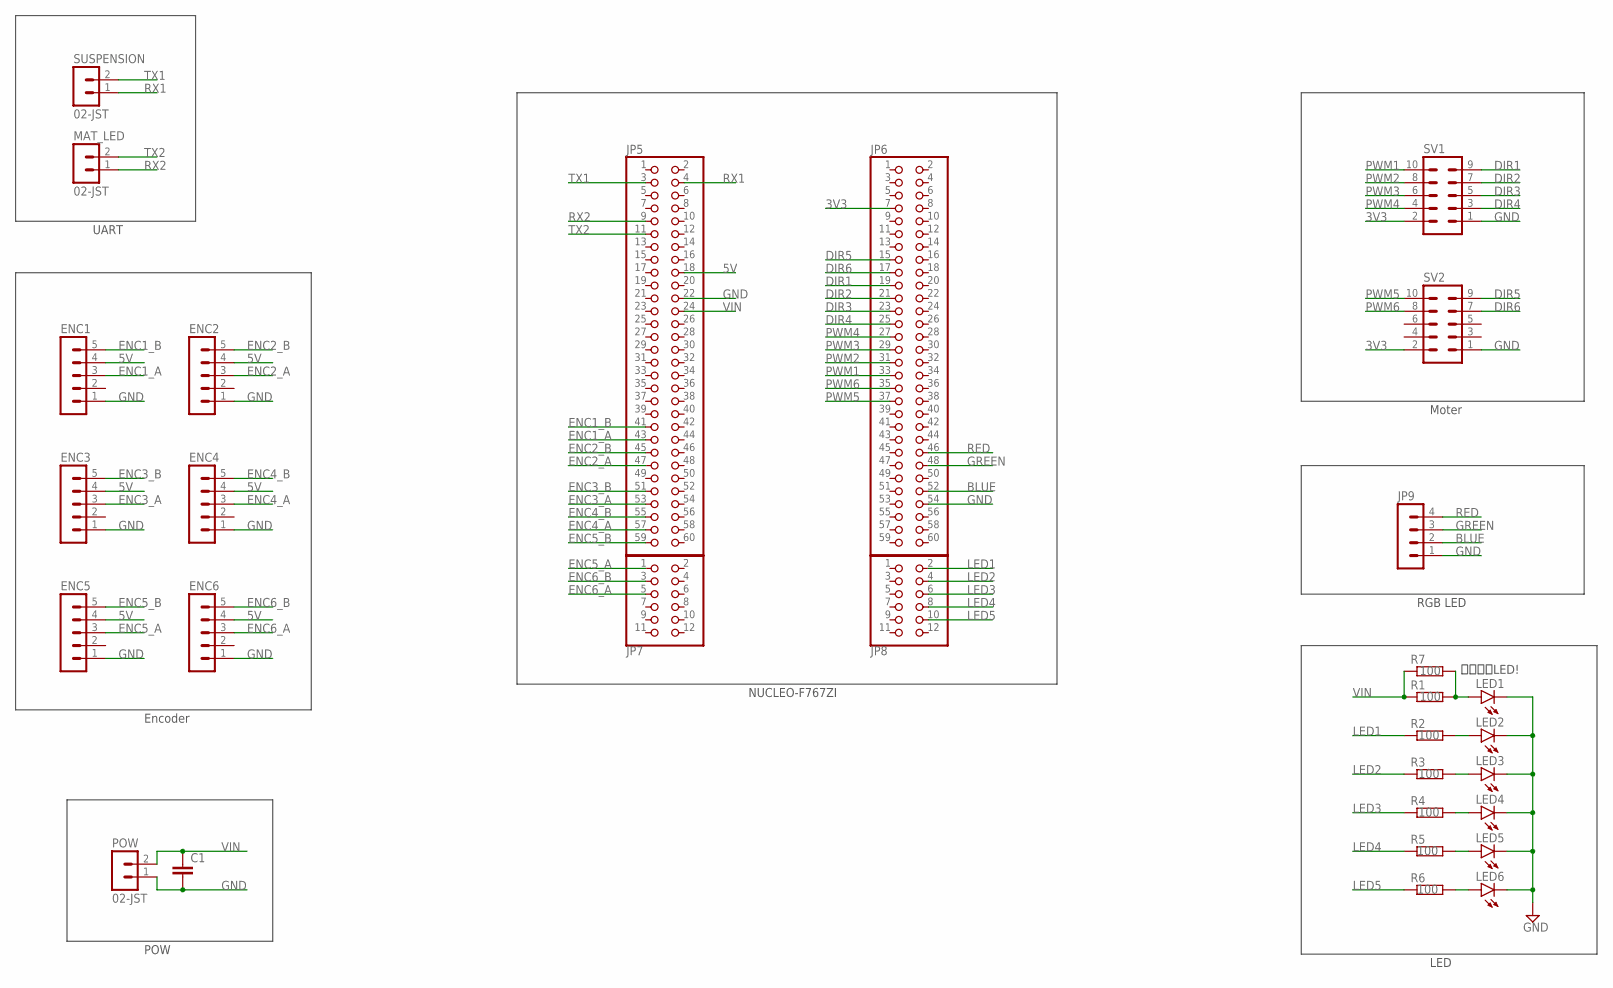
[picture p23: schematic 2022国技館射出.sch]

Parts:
C1: C-EU025-024X044; C025-024X044
ENC1, ENC2, ENC3, ENC4, ENC5, ENC6: 05-JST; B5B-XH
JP5, JP6: PINHD-2X30; 2X30
JP7, JP8: PINHD-2X6; 2X06
JP9: 04-JST; B4B-XH
LED1, LED2, LED3, LED4, LED5, LED6: LED5MM
MAT_LED: 02-JST; B2B-XH
POW: 02-JST; B2B-XH
R1, R2, R3, R4, R5, R6, R7: 100; 0204/7
SUSPENSION: 02-JST; B2B-XH
SV1, SV2: ML10

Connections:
3V3: JP6.7, SV1.2, SV2.2
5V: ENC1.4, ENC2.4, ENC3.4, ENC4.4, ENC5.4, ENC6.4, JP5.18
BLUE: JP6.52, JP9.2
DIR1: JP6.19, SV1.9
DIR2: JP6.21, SV1.7
DIR3: JP6.23, SV1.5
DIR4: JP6.25, SV1.3
DIR5: JP6.15, SV2.9
DIR6: JP6.17, SV2.7
ENC1_A: ENC1.3, JP5.43
ENC1_B: ENC1.5, JP5.41
ENC2_A: ENC2.3, JP5.47
ENC2_B: ENC2.5, JP5.45
ENC3_A: ENC3.3, JP5.53
ENC3_B: ENC3.5, JP5.51
ENC4_A: ENC4.3, JP5.57
ENC4_B: ENC4.5, JP5.55
ENC5_A: ENC5.3, JP7.1
ENC5_B: ENC5.5, JP5.59
ENC6_A: ENC6.3, JP7.5
ENC6_B: ENC6.5, JP7.3
GND: C1.2, ENC1.1, ENC2.1, ENC3.1, ENC4.1, ENC5.1, ENC6.1, JP5.22, JP6.54, JP9.1, LED1.K (C), LED2.K (C), LED3.K (C), LED4.K (C), LED5.K (C), LED6.K (C), POW.1, SV1.1, SV2.1
GREEN: JP6.48, JP9.3
LED1: JP8.2, R2.1
LED2: JP8.4, R3.1
LED3: JP8.6, R4.1
LED4: JP8.8, R5.1
LED5: JP8.10, R6.1
unnamed: LED1.A, R1.2, R7.2
unnamed: LED2.A, R2.2
unnamed: LED3.A, R3.2
unnamed: LED4.A, R4.2
unnamed: LED5.A, R5.2
unnamed: LED6.A, R6.2
PWM1: JP6.33, SV1.10
PWM2: JP6.31, SV1.8
PWM3: JP6.29, SV1.6
PWM4: JP6.27, SV1.4
PWM5: JP6.37, SV2.10
PWM6: JP6.35, SV2.8
RED: JP6.46, JP9.4
RX1: JP5.4, SUSPENSION.1
RX2: JP5.9, MAT_LED.1
TX1: JP5.3, SUSPENSION.2
TX2: JP5.11, MAT_LED.2
VIN: C1.1, JP5.24, POW.2, R1.1, R7.1

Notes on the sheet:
NUCLEO-F767ZI
Encoder
Moter
POW
UART
RGB LED
超高輝度LED!
LED

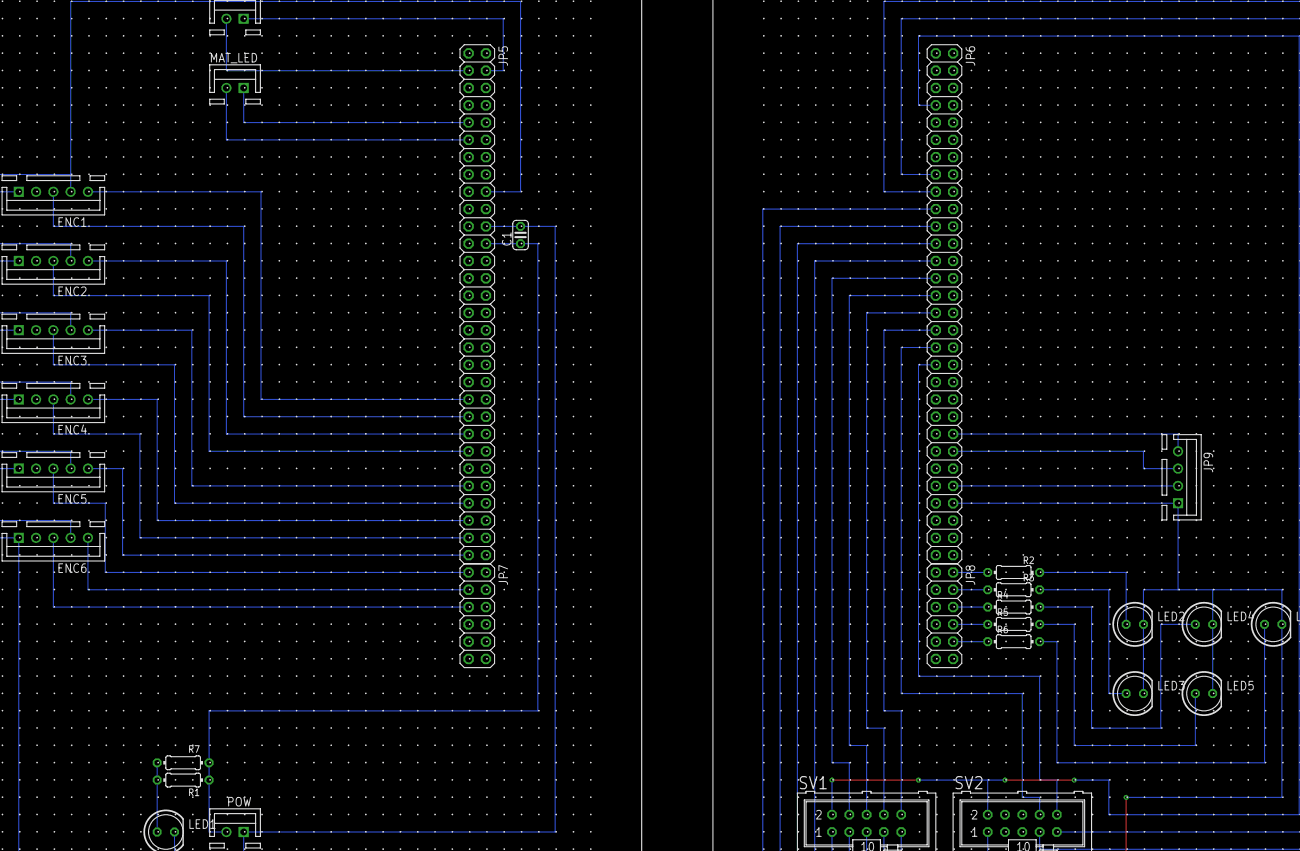
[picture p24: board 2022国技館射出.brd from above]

Board: 2 copper layers, 32 parts (0 on the bottom side), 46 nets.

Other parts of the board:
U$1, U$2: TYPE.A

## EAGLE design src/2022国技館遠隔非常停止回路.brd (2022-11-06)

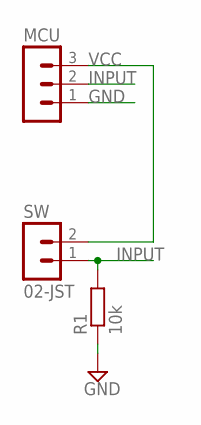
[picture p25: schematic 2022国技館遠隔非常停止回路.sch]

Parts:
MCU: 03-JST; B3B-XH
R1: 10k; 0204/7
SW: 02-JST; B2B-XH

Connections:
GND: MCU.1, R1.1
INPUT: MCU.2, R1.2, SW.1
VCC: MCU.3, SW.2

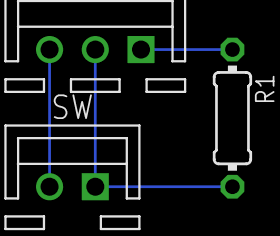
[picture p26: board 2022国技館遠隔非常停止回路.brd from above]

Board: 2 copper layers, 4 parts (0 on the bottom side), 3 nets.

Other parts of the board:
U$1: TYPE.C

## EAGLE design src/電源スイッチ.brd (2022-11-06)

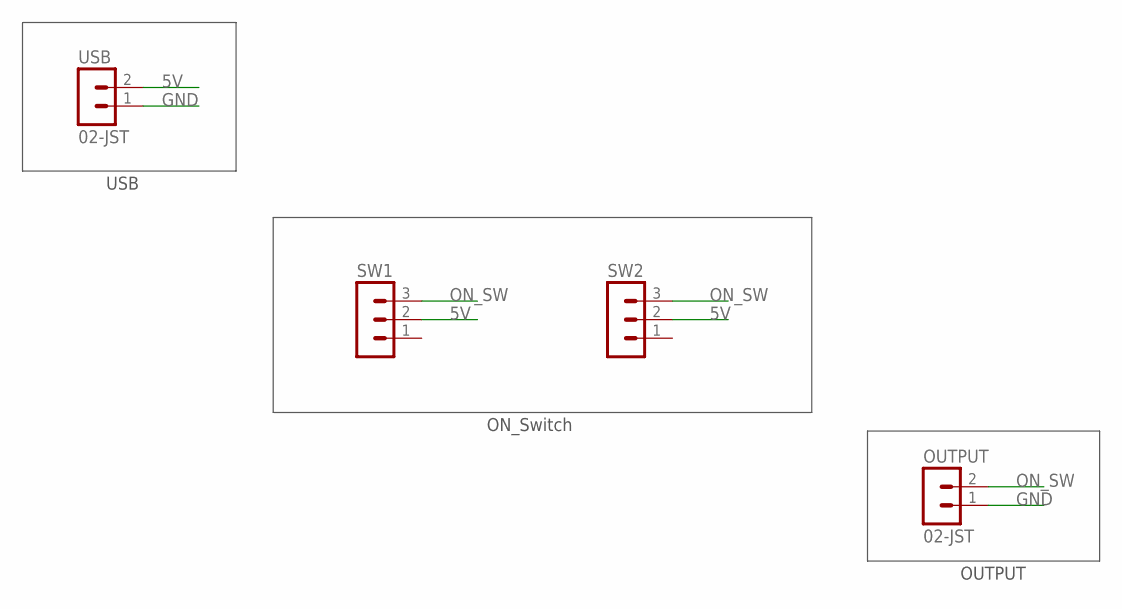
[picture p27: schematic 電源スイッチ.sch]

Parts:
OUTPUT: 02-JST; B2B-XH
SW1, SW2: 03-JST; B3B-XH
USB: 02-JST; B2B-XH

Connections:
5V: SW1.2, SW2.2, USB.2
GND: OUTPUT.1, USB.1
ON_SW: OUTPUT.2, SW1.3, SW2.3

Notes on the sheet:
USB
ON_Switch
OUTPUT

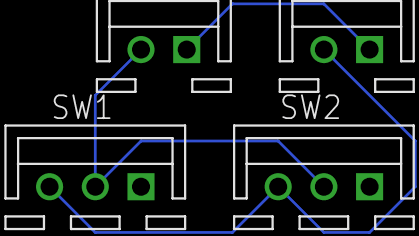
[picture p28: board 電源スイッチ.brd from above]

Board: 2 copper layers, 5 parts (0 on the bottom side), 3 nets.

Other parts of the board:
U$1: TYPE.C

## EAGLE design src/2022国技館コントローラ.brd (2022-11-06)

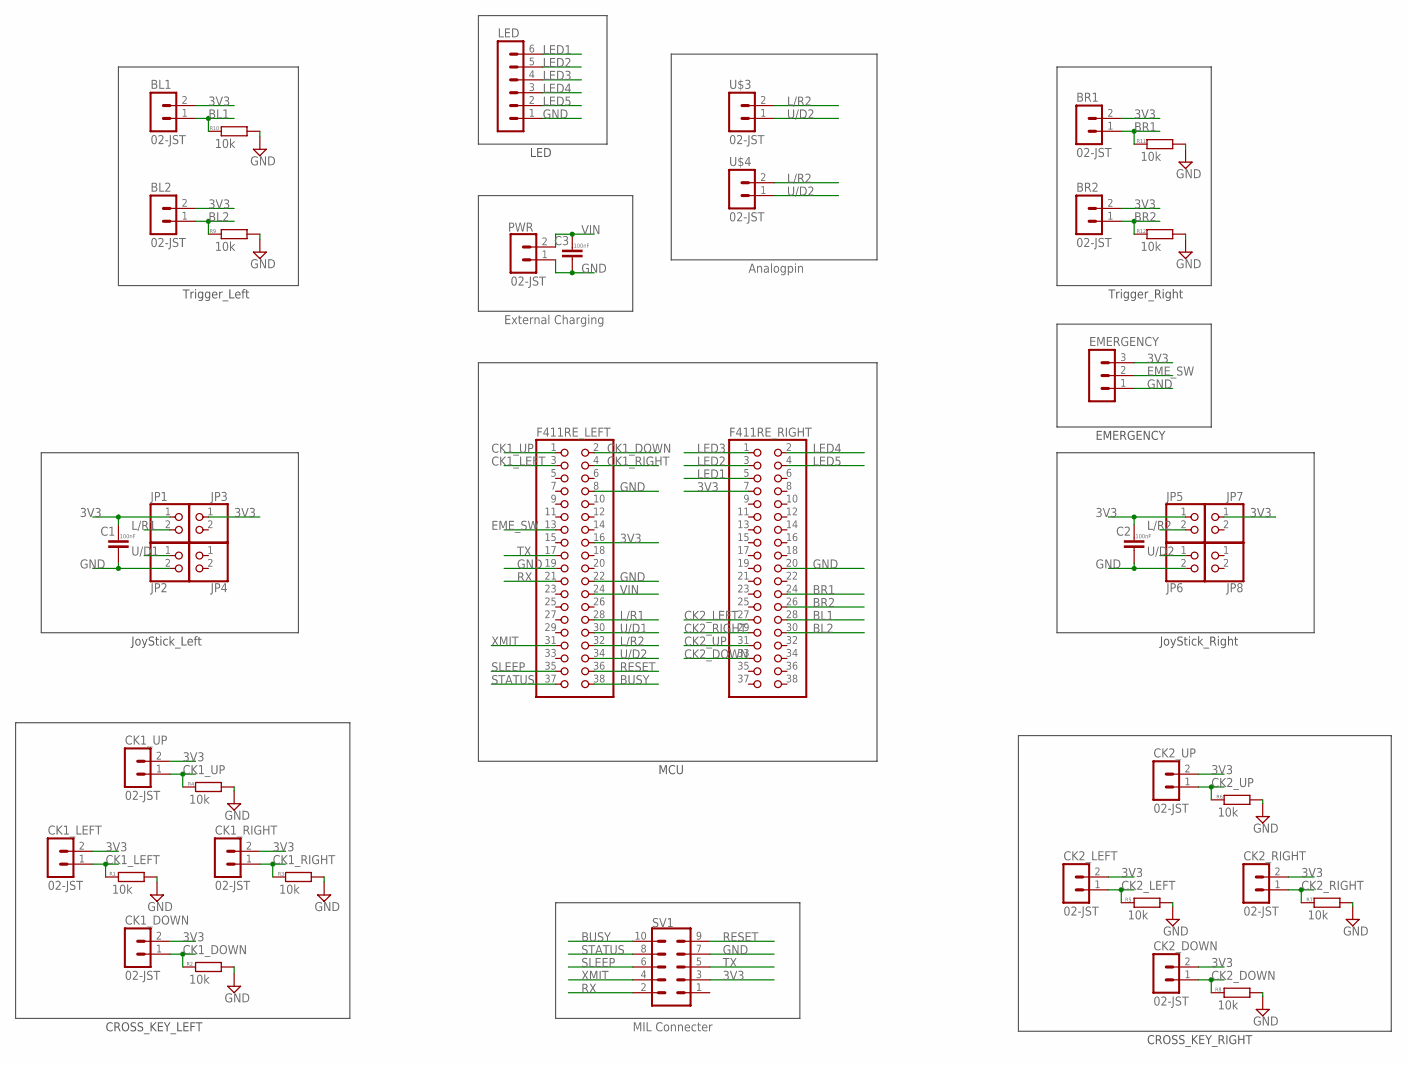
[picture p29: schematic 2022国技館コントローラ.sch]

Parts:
BL1, BL2: 02-JST; B2B-XH
BR1, BR2: 02-JST; B2B-XH
C1, C2, C3: 100nF; C025-024X044
CK1_DOWN, CK1_LEFT, CK1_RIGHT, CK1_UP, CK2_DOWN, CK2_LEFT, CK2_RIGHT, CK2_UP: 02-JST; B2B-XH
EMERGENCY: 03-JST; B3B-XH
F411RE_LEFT, F411RE_RIGHT: PINHD-2X19; 2X19
JP1, JP2, JP3, JP4, JP5, JP6, JP7, JP8: PINHD-1X2; 1X02
LED: 06-JST; B6B-XH
PWR: 02-JST; B2B-XH
R1, R2, R3, R4, R5, R6, R7, R8, R9, R10, R11, R12: 10k; 0204/7
SV1: ML10
U$3, U$4: 02-JST; B2B-XH

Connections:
3V3: BL1.2, BL2.2, BR1.2, BR2.2, C1.1, C2.1, CK1_DOWN.2, CK1_LEFT.2, CK1_RIGHT.2, CK1_UP.2, CK2_DOWN.2, CK2_LEFT.2, CK2_RIGHT.2, CK2_UP.2, EMERGENCY.3, F411RE_LEFT.16, F411RE_RIGHT.7, JP1.1, JP3.1, JP5.1, JP7.1, SV1.3
BL1: BL1.1, F411RE_RIGHT.28, R10.1
BL2: BL2.1, F411RE_RIGHT.30, R9.1
BR1: BR1.1, F411RE_RIGHT.24, R11.1
BR2: BR2.1, F411RE_RIGHT.26, R12.1
BUSY: F411RE_LEFT.38, SV1.10
CK1_DOWN: CK1_DOWN.1, F411RE_LEFT.2, R2.1
CK1_LEFT: CK1_LEFT.1, F411RE_LEFT.3, R1.1
CK1_RIGHT: CK1_RIGHT.1, F411RE_LEFT.4, R3.1
CK1_UP: CK1_UP.1, F411RE_LEFT.1, R4.1
CK2_DOWN: CK2_DOWN.1, F411RE_RIGHT.33, R8.1
CK2_LEFT: CK2_LEFT.1, F411RE_RIGHT.27, R5.1
CK2_RIGHT: CK2_RIGHT.1, F411RE_RIGHT.29, R7.1
CK2_UP: CK2_UP.1, F411RE_RIGHT.31, R6.1
EME_SW: EMERGENCY.2, F411RE_LEFT.13
GND: C1.2, C2.2, C3.2, EMERGENCY.1, F411RE_LEFT.8, F411RE_LEFT.19, F411RE_LEFT.22, F411RE_RIGHT.20, JP2.2, JP6.2, LED.1, PWR.1, R1.2, R2.2, R3.2, R4.2, R5.2, R6.2, R7.2, R8.2, R9.2, R10.2, R11.2, R12.2, SV1.7
L/R1: F411RE_LEFT.28, JP1.2
L/R2: F411RE_LEFT.32, JP5.2, U$3.2, U$4.2
LED1: F411RE_RIGHT.5, LED.6
LED2: F411RE_RIGHT.3, LED.5
LED3: F411RE_RIGHT.1, LED.4
LED4: F411RE_RIGHT.2, LED.3
LED5: F411RE_RIGHT.4, LED.2
RESET: F411RE_LEFT.36, SV1.9
RX: F411RE_LEFT.21, SV1.2
SLEEP: F411RE_LEFT.35, SV1.6
STATUS: F411RE_LEFT.37, SV1.8
TX: F411RE_LEFT.17, SV1.5
U/D1: F411RE_LEFT.30, JP2.1
U/D2: F411RE_LEFT.34, JP6.1, U$3.1, U$4.1
VIN: C3.1, F411RE_LEFT.24, PWR.2
XMIT: F411RE_LEFT.31, SV1.4

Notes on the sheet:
JoyStick_Left
JoyStick_Right
MCU
CROSS_KEY_LEFT
CROSS_KEY_RIGHT
Trigger_Left
Trigger_Right
External Charging
MIL Connecter
LED
Analogpin
EMERGENCY

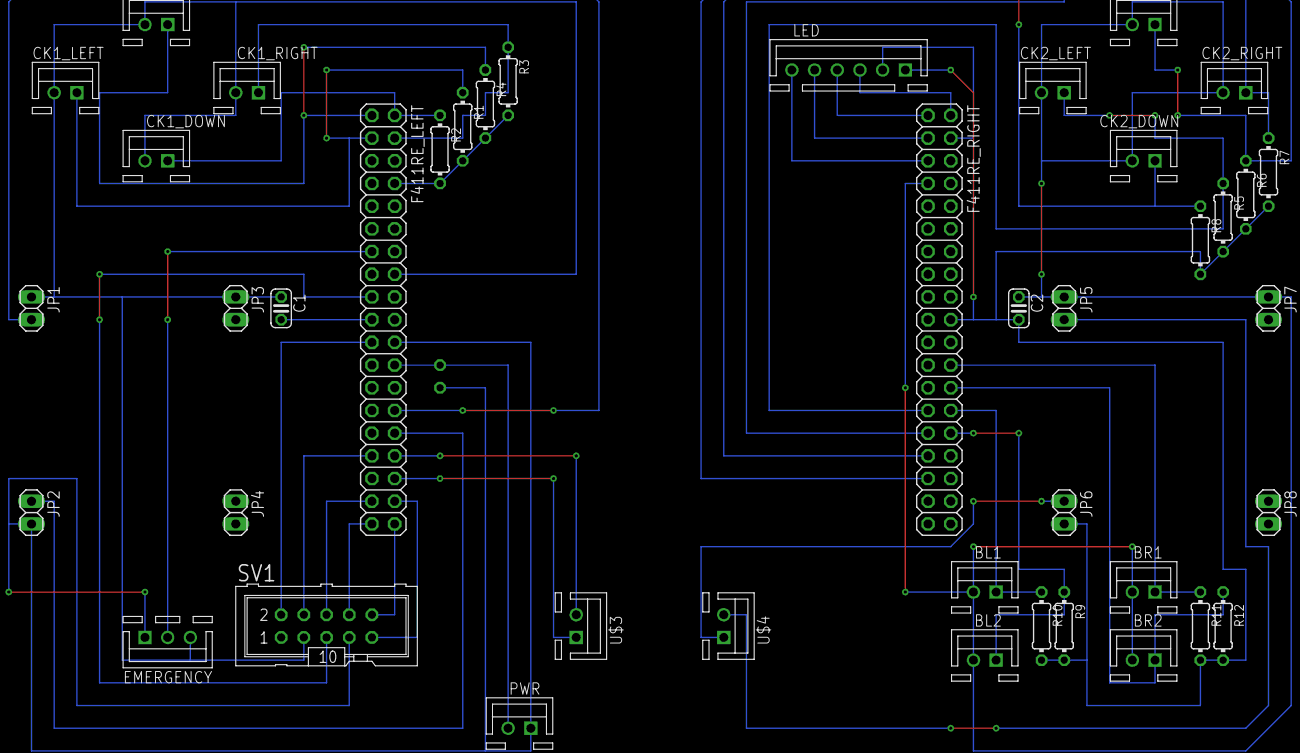
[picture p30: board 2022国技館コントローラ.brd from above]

Board: 2 copper layers, 45 parts (1 on the bottom side), 32 nets.

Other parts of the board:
U$1, U$2: TYPE.B

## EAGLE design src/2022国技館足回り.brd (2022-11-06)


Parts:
C1: 100nF; C025-024X044
JP1, JP2: PINHD-2X19; 2X19
JP3, JP4, JP5, JP6: 05-JST; B5B-XH
JP8, JP9: PINHD-1X8; 1X08
LED1, LED2, LED3, LED4, LED5, LED6: LED5MM
POW: 02-JST; B2B-XH
R1: 100; 0204/7
R2, R3, R4, R5, R6: 100; 0207/2V
REMOTE_SW: 02-JST; B2B-XH
SUSPENSION: 02-JST; B2B-XH
SV1: ML10

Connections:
3V3: JP1.16, JP8.7, SV1.2
5V: JP1.18, JP3.4, JP4.4, JP5.4, JP6.4
BUSY: JP1.38, JP8.1
DIR1: JP2.34, SV1.9
DIR2: JP2.16, SV1.7
DIR3: JP2.6, SV1.5
DIR4: JP2.4, SV1.3
EMERGENCY: JP2.2, REMOTE_SW.2
ENC1_A: JP1.15, JP3.3
ENC1_B: JP1.13, JP3.5
ENC2_A: JP1.3, JP4.3
ENC2_B: JP1.1, JP4.5
ENC3_A: JP2.3, JP5.3
ENC3_B: JP2.5, JP5.5
ENC4_A: JP1.37, JP6.3
ENC4_B: JP1.35, JP6.5
GND: C1.2, JP1.20, JP3.1, JP4.1, JP5.1, JP6.1, JP9.8, LED1.K (C), LED2.K (C), LED3.K (C), LED4.K (C), LED5.K (C), LED6.K (C), POW.1, REMOTE_SW.1, SV1.1
LED1: JP2.22, R2.1
LED2: JP2.24, R3.1
LED3: JP2.26, R4.1
LED4: JP2.28, R5.1
LED5: JP2.30, R6.1
unnamed: LED3.A, R3.2
unnamed: LED2.A, R2.2
unnamed: LED1.A, R1.2
unnamed: LED6.A, R6.2
unnamed: LED5.A, R5.2
unnamed: LED4.A, R4.2
PWM1: JP2.25, SV1.10
PWM2: JP2.23, SV1.8
PWM3: JP2.21, SV1.6
PWM4: JP2.19, SV1.4
RESET: JP1.32, JP8.8
RX1: JP1.21, JP8.4
RX2: JP2.14, SUSPENSION.1
SLEEP: JP1.30, JP9.2
STATUS: JP1.34, JP8.6
TX1: JP1.17, JP9.3
TX2: JP2.12, SUSPENSION.2
VIN: C1.1, JP1.24, POW.2, R1.1
XMIT: JP1.36, JP8.2

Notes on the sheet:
Encoder
UART
Moter
IM920sL
POW
NUCLEO-F411RE
LED
EMERGENCY


Board: 2 copper layers, 26 parts (1 on the bottom side), 41 nets.

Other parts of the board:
U$1: TYPE.A

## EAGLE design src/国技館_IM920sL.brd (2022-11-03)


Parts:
JP1, JP2: PINHD-1X8; 1X08
SV1: ML10

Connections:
3V3: JP1.7, SV1.3
BUSY: JP1.1, SV1.10
GND: JP2.8, SV1.7
RESET: JP1.8, SV1.9
RX: JP2.3, SV1.2
SLEEP: JP2.2, SV1.6
STATUS: JP1.6, SV1.8
TX: JP1.4, SV1.5
XMIT: JP1.2, SV1.4

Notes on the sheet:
IM920sL
MIL


Board: 2 copper layers, 4 parts (0 on the bottom side), 9 nets.

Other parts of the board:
U$1: TYPE.C

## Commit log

2022-07-12 [add]srcの追加
    [[仮]コントローラー.sch]
2022-07-12 [add]メイン回路の追加
    [[仮]メイン回路.sch]
2022-07-12 [add]メイン回路 Issaimaru側の追加
    [[仮]コントローラー.sch, [仮]メイン回路.sch, メイン回路 Issaimaru側.sch]
2022-07-13 [add]コントローラー回路図の追加，メイン基板続き
    [コントローラ.sch, メイン回路 Issaimaru側.brd, メイン回路 Issaimaru側.sch]
2022-07-29 [add]main kairo Aoi
    [メイン回路.sch]
2022-08-02 [add]コントローラに対する進捗dxを生成✅
    [コントローラ.brd, コントローラ.sch]
2022-08-02 [add]コントローラー.brdの追加
    [コントローラ.brd, コントローラ.sch]
2022-08-02 [fix]コントローラー.brdの修正
    [コントローラ.brd]
2022-08-04 [add]メイン回路
    [メイン回路１.brd, メイン回路１.sch, メイン回路２.brd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]
2022-08-04 [add]コントローラ
    [[仮]コントローラー.sch, [仮]メイン回路.sch, コントローラ.brd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]
2022-08-17 [move]ファイルの移動
    [メイン回路 Issaimaru側.brd, メイン回路 Issaimaru側.sch, メイン回路１.brd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]
2022-08-18 メイン回路
    [メイン回路１.brd, メイン回路１.sch]
2022-08-18 [fix]受信側の回路のsch修正全て
    [メイン回路１.brd, メイン回路１.sch, メイン回路２.brd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]
2022-08-18 [fix]brd途中まで変更
    [メイン回路２.brd, メイン回路２.sch]
2022-08-19 [complete]メイン回路2の完成
    [メイン回路２.brd, メイン回路２.sch]
2022-08-19 [fix]メイン回路2.schの修正
    [メイン回路２.sch]
2022-08-19 [complete]メイン回路1の完成
    [メイン回路１.brd, メイン回路１.sch, メイン回路２.brd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]
2022-08-21 [add]暴走対策回路の追加--ここから--
    [メイン回路１.brd, メイン回路１.sch]
2022-08-21 [complete]メイン回路1の暴走対策回路の配線完了
    [メイン回路１.brd]
2022-08-22 [add]メイン回路1にソケット置きを追加
    [メイン回路１.brd, メイン回路１.sch]
2022-08-22 [fix]接続問題の解消
    [メイン回路１.brd, メイン回路１.sch]
2022-08-22 [fix]メイン回路1にソケット置きを追加
    [メイン回路１.brd]
2022-08-22 [complete]メイン回路2に暴走対策回路を追加
    [メイン回路２.brd, メイン回路２.sch]
2022-08-22 暴走対策機能付き非常停止スイッチ
    [暴走対策機能付き非常停止スイッチ.brd, 暴走対策機能付き非常停止スイッチ.sch]
2022-08-30 [add]コントローラAoi
    [コントローラ.brd, コントローラ.sch]
2022-08-31 暴走対策機能付き非常停止スイッチの回路のガバを修復
    [メイン回路１.brd, メイン回路１.sch, 暴走対策機能付き非常停止スイッチ.brd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]
2022-08-31 回路図の追加
2022-08-31 [add]コントローラ Aoi
    [コントローラ.brd, コントローラ.sch]
2022-09-23 配線をDriveUnit ver2.0用に変更
    [メイン回路１.brd, メイン回路１.sch]
2022-09-30 エンコーダー回路追加
    [上部機構用エンコーダ.brd, 上部機構用エンコーダ.sch]
2022-10-01 上部機構用エンコーダー 回路の微修正
    [上部機構用エンコーダ.brd, 上部機構用エンコーダ.sch]
2022-10-30 国技館コントローラの追加
    [2022国技館コントローラ.brd, 2022国技館コントローラ.sch, コントローラ.brd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]
2022-10-31 「ｋ」コントローラ
    [2022国技館コントローラ.brd, 2022国技館コントローラ.sch]
2022-11-01 国技館コントローラ_配線の修正
    [2022国技館コントローラ.brd, 2022国技館コントローラ.sch]
2022-11-01 [k]コントローラ
    [2022国技館コントローラ.brd, 2022国技館コントローラ.sch]
2022-11-01 足回りなど
    [2022国技館射出.brd, 2022国技館射出.sch, 2022国技館足回り.brd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]
2022-11-02 国技館足回り回路の追加
    [2022国技館射出.brd, 2022国技館射出.sch, 2022国技館足回り.brd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]
2022-11-03 2022国技館射出完成
    [2022国技館射出.brd, 2022国技館射出.sch]
2022-11-03 LEDsの追加
    [2022国技館LEDs.brd, 2022国技館LEDs.sch, 国技館_IM920sL.sch]
2022-11-03 足回りコントローラ
    [2022国技館コントローラ.brd, 2022国技館足回り.brd, 2022国技館足回り.sch]
2022-11-03 国技館_IM920sLの追加
    [国技館_IM920sL.brd]
2022-11-03 助けてー進捗に襲われてまーす
2022-11-06 国技館足回り修正前
    [2022国技館コントローラ.brd, 2022国技館コントローラ.sch, 2022国技館足回り.brd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]
2022-11-06 国技館足回り修正後
    [2022国技館足回り.brd, 2022国技館足回り.sch]
2022-11-06 11/06日の進捗
    [電源スイッチ.brd, 電源スイッチ.sch]
2022-11-08 11/08修正
    [2022国技館射出.brd]
